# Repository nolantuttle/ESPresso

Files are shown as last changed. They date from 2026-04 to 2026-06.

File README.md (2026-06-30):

# ESPresso

Custom ESP32-C3 Supermini controller for the Gaggia Classic Pro. Handles boiler PID via SSR, shot timing, brew switch sense, and future pump PWM pressure profiling via MOC3021 + BTA41-600B TRIAC. Built with the Arduino framework.

## Hardware

| Component | Detail |
|---|---|
| MCU | ESP32-C3 Supermini (22×18mm, GPIOs 0–10, 20, 21) |
| Boiler control | Fotek 25DA SSR on GPIO10 via 330Ω |
| Thermocouple | MAX31855 on GPIOs 4 (SCK), 5 (MISO), 7 (CS) |
| Display | SSD1306 128×64 OLED on I2C, GPIOs 8 (SDA), 9 (SCL) |
| Pump control | MOC3021 + BTA41-600B TRIAC, GPIO2 PWM (pending MOC3041 + snubber) |
| Brew sense | Dry contact on second side of brew switch, GPIO1, 10kΩ pullup, active low |
| Pressure | XDB401 0–1.2MPa via 10kΩ/20kΩ divider → GPIO6 (not yet wired) |
| Mode toggle | Momentary to GND on GPIO20, firmware latched |
| Temp buttons | Resistor ladder on GPIO21 — up 10kΩ, down 47kΩ, 10kΩ pullup |
| Pot wiper | GPIO3, replacement pot coming (100nF cap to GND) |

# Electrical Schematic


## Firmware Features

- **Boiler PID** — Kp=38, Ki=4, Kd=250, 2s cycle time, SSR on GPIO10
- **Brew/steam modes** — toggle GPIO20; brew 185–220°F (default 205°F), steam 250–300°F (default 280°F)
- **Shot timer** — starts on brew switch close, stops on open, displayed live on OLED
- **Temp adjustment** — resistor ladder buttons ±1°F per press, long-press temp-up for settings stub
- **OLED** — mode, boiler state, current temp (large), setpoint, PID on-time, shot timer / error

## Pin Map

| GPIO | Function | Status |
|---|---|---|
| 0 | free | — |
| 1 | Brew switch sense | wired |
| 2 | MOC3041 PWM out | wired |
| 3 | free | — |
| 4 | MAX31855 SCK | wired |
| 5 | MAX31855 MISO | wired |
| 6 | Pressure transducer ADC | wired |
| 7 | MAX31855 CS | wired |
| 8 | OLED SDA | wired |
| 9 | OLED SCL | wired |
| 10 | SSR boiler out | wired |
| 20 | Mode toggle button | wired |
| 21 | Resistor ladder buttons | wired |

## Repository Contents
    /ESPresso    — Arduino sketch (ESP32-C3)
    /docs        — wiring notes and schematic

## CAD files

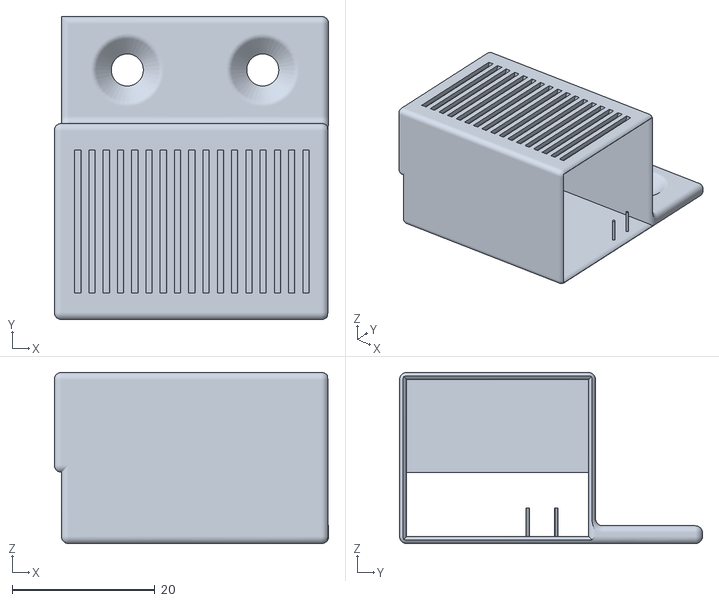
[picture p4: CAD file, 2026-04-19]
buck_module_case.STL
38.5 x 42.5 x 24.0

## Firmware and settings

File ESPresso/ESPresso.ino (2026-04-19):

#include <Wire.h>
#include <Adafruit_GFX.h>
#include <Adafruit_SSD1306.h>
#include <Adafruit_MAX31855.h>
#include <PID_v1.h>

// ─── Display ───────────────────────────────────────────────
#define SCREEN_WIDTH  128
#define SCREEN_HEIGHT 64
#define SCREEN_ADDRESS 0x3C
Adafruit_SSD1306 display(SCREEN_WIDTH, SCREEN_HEIGHT, &Wire, -1);

// ─── Pin definitions ───────────────────────────────────────
const int SPI_CLK_PIN  = 4;   // MAX31855 SCK
const int SPI_MISO_PIN = 5;   // MAX31855 DO
const int CS_PIN       = 7;   // MAX31855 CS
const int SDA_PIN      = 8;   // OLED SDA
const int SCL_PIN      = 9;   // OLED SCL
const int BOILER_PIN   = 10;  // SSR control
const int TOGGLE_PIN   = 20;  // Mode toggle button, pullup, closes to GND
const int ADC_BUTTONS  = 21;  // Resistor ladder: temp up (10kΩ) + temp down (47kΩ)
const int PUMP_PIN     = 2;   // MOC3021 PWM out
// const int ADC_POT      = 6;  // Pot wiper — not yet wired (pot snapped)
const int BREW_SENSE      = 1;   // Dry contact closure, 10kΩ pullup to 3.3V, active low
// const int ADC_PRESSURE = 2;  // Pressure transducer — not yet wired

// ─── Thermocouple ──────────────────────────────────────────
Adafruit_MAX31855 thermocouple(SPI_CLK_PIN, CS_PIN, SPI_MISO_PIN);

// ─── PID ───────────────────────────────────────────────────
// Kd bumped 180→280 to dampen 5-10F warmup overshoot
// If still overshooting: increase Kd toward 350-400
// If response near setpoint feels sluggish: back Kd toward 220
double BOILER_SETPOINT = 205.0;
double CURRENT_TEMP    = 0.0;
double PID_OUTPUT      = 0.0;
double Kp = 38, Ki = 4, Kd = 250;

unsigned long previousTime = 0;
unsigned long cycleTime    = 2000;
unsigned long offTime      = 0;
bool BOILER_ON             = false;

PID mainPID(&CURRENT_TEMP, &PID_OUTPUT, &BOILER_SETPOINT, Kp, Ki, Kd, DIRECT);

// ─── Mode ──────────────────────────────────────────────────
bool STEAM_ON = false;

const double BREW_SETPOINT_DEFAULT  = 205.0;
const double STEAM_SETPOINT_DEFAULT = 280.0;
const double BREW_SETPOINT_MIN      = 185.0;
const double BREW_SETPOINT_MAX      = 220.0;
const double STEAM_SETPOINT_MIN     = 250.0;
const double STEAM_SETPOINT_MAX     = 300.0;

// ─── Shot timer ────────────────────────────────────────────
bool brewActive                = false;
bool lastBrewRaw               = HIGH;
unsigned long brewStartTime    = 0;
unsigned long shotElapsed      = 0;   // ms, frozen at shot end
bool shotDone                  = false;

// ─── Display timing ────────────────────────────────────────
unsigned long lastDisplayUpdate      = 0;
const unsigned long DISPLAY_INTERVAL = 2000;

// ─── Button ladder ADC thresholds ──────────────────────────
// Temp up (left):     10kΩ to GND → ~1.65V → ADC ~2048
// Temp down (center): 47kΩ to GND → ~2.77V → ADC ~3440
// Nothing pressed:    floating high          → ADC ~4095
const int THRESH_TEMPUP_LO   = 1500;
const int THRESH_TEMPUP_HI   = 2600;
const int THRESH_TEMPDOWN_LO = 2700;
const int THRESH_TEMPDOWN_HI = 3800;

// ─── Button state ──────────────────────────────────────────
bool lastToggleRaw                 = HIGH;
unsigned long toggleDebounce       = 0;
const unsigned long TOGGLE_DEBOUNCE_MS = 50;

bool tempUpPressed                 = false;
bool tempDownPressed               = false;
unsigned long leftButtonHoldStart  = 0;
bool settingsStubFired             = false;
unsigned long lastTempUpDebounce   = 0;
unsigned long lastTempDownDebounce = 0;
const unsigned long DEBOUNCE_MS    = 50;
const unsigned long LONG_PRESS_MS  = 2000;

// ─── Setup ─────────────────────────────────────────────────
void setup() {

  Serial.begin(115200);

  Wire.begin(SDA_PIN, SCL_PIN);

  pinMode(CS_PIN, OUTPUT);
  digitalWrite(CS_PIN, HIGH);

  pinMode(BOILER_PIN, OUTPUT);
  digitalWrite(BOILER_PIN, LOW);

  pinMode(TOGGLE_PIN, INPUT_PULLUP);
  pinMode(BREW_SENSE, INPUT_PULLUP);

  ledcAttach(PUMP_PIN, 60, 8);

  mainPID.SetMode(AUTOMATIC);
  mainPID.SetOutputLimits(0, cycleTime);
  mainPID.SetSampleTime(1000);

  delay(500);

  if (!display.begin(SSD1306_SWITCHCAPVCC, SCREEN_ADDRESS)) {
    Serial.println(F("SSD1306 allocation failed"));
    for (;;);
  }

  startupScreen();
  delay(1500);
  display.clearDisplay();
}

void pumpOn(int duty){
  ledcWrite(PUMP_PIN, duty);
}

void pumpOff(){
  ledcWrite(PUMP_PIN, 0);
}

// ─── Loop ──────────────────────────────────────────────────
void loop() {
  readToggle();
  readButtons();
  readBrewSense();

  CURRENT_TEMP = thermocouple.readFahrenheit() - 10;

  mainPID.Compute();

  unsigned long now = millis();

  if (!BOILER_ON && now - previousTime >= cycleTime) {
    previousTime = now;
    offTime = now + (unsigned long)PID_OUTPUT;
    BOILER_ON = true;
    digitalWrite(BOILER_PIN, HIGH);
  }

  if (BOILER_ON && now >= offTime) {
    digitalWrite(BOILER_PIN, LOW);
    BOILER_ON = false;
  }

  unsigned long displayInterval = brewActive ? 500UL : DISPLAY_INTERVAL;
  if (now - lastDisplayUpdate >= displayInterval) {
    lastDisplayUpdate = now;
    mainDisplay();
  }
}

// ─── Toggle reading (GPIO20, firmware latched) ─────────────
void readToggle() {
  unsigned long now = millis();
  bool raw = digitalRead(TOGGLE_PIN);

  if (lastToggleRaw == HIGH && raw == LOW) {
    if (now - toggleDebounce > TOGGLE_DEBOUNCE_MS) {
      STEAM_ON = !STEAM_ON;
      BOILER_SETPOINT = STEAM_ON ? STEAM_SETPOINT_DEFAULT : BREW_SETPOINT_DEFAULT;
      resetPID();
      toggleDebounce = now;
    }
  }

  lastToggleRaw = raw;
}

// ─── Button ladder reading (GPIO21) ────────────────────────
void readButtons() {
  unsigned long now = millis();
  int raw = analogRead(ADC_BUTTONS);

  // Uncomment to debug ADC values:
  // Serial.println(raw);

  // ── Temp up (left button) ──
  bool tempUpNow = (raw >= THRESH_TEMPUP_LO && raw < THRESH_TEMPUP_HI);

  if (tempUpNow && !tempUpPressed) {
    leftButtonHoldStart = now;
    settingsStubFired = false;
    lastTempUpDebounce = now;
  }

  if (tempUpNow && !settingsStubFired) {
    if (now - leftButtonHoldStart >= LONG_PRESS_MS) {
      settingsStubFired = true;
      enterSettingsStub();
    }
  }

  if (!tempUpNow && tempUpPressed && !settingsStubFired) {
    if (now - lastTempUpDebounce > DEBOUNCE_MS) {
      adjustSetpoint(1.0);
    }
  }

  tempUpPressed = tempUpNow;

  // ── Temp down (center button) ──
  bool tempDownNow = (raw >= THRESH_TEMPDOWN_LO && raw < THRESH_TEMPDOWN_HI);

  if (tempDownNow && !tempDownPressed) {
    lastTempDownDebounce = now;
  }

  if (!tempDownNow && tempDownPressed) {
    if (now - lastTempDownDebounce > DEBOUNCE_MS) {
      adjustSetpoint(-1.0);
    }
  }

  tempDownPressed = tempDownNow;
}

// ─── Setpoint adjustment ───────────────────────────────────
void adjustSetpoint(double delta) {
  BOILER_SETPOINT += delta;
  if (STEAM_ON) {
    BOILER_SETPOINT = constrain(BOILER_SETPOINT, STEAM_SETPOINT_MIN, STEAM_SETPOINT_MAX);
  } else {
    BOILER_SETPOINT = constrain(BOILER_SETPOINT, BREW_SETPOINT_MIN, BREW_SETPOINT_MAX);
  }
}

// ─── PID reset ─────────────────────────────────────────────
void resetPID() {
  mainPID.SetMode(MANUAL);
  PID_OUTPUT = 0;
  mainPID.SetMode(AUTOMATIC);
}

// ─── Settings stub ─────────────────────────────────────────
void enterSettingsStub() {
  // TODO: implement settings menu
  // Suggested: Kp, Ki, Kd tuning, brew/steam setpoint defaults,
  // PID cycle time, temp offset calibration
  Serial.println(F("Settings mode triggered (not yet implemented)"));
}

// ─── Brew sense + shot timer (GPIO1, active low) ───────────
void readBrewSense() {
  bool raw = digitalRead(BREW_SENSE);

  if (lastBrewRaw == HIGH && raw == LOW) {
    brewActive = true;
    brewStartTime = millis();
    shotDone = false;
    pumpOn(180); // start pump immediately on switch close
} else if (lastBrewRaw == LOW && raw == HIGH) {
    brewActive = false;
    shotElapsed = millis() - brewStartTime;
    shotDone = true;
    pumpOff(); // stop pump immediately on switch open
}

  lastBrewRaw = raw;
}

// ─── Startup screen ────────────────────────────────────────
void startupScreen() {
  display.clearDisplay();
  display.setTextColor(SSD1306_WHITE);
  display.setTextSize(2);
  display.setCursor(10, 10);
  display.println(F("ESPresso"));
  display.setTextSize(1);
  display.setCursor(28, 38);
  display.println(F("warming up..."));
  display.display();
}

// ─── Main display ──────────────────────────────────────────
void mainDisplay() {
  display.clearDisplay();
  display.setTextColor(SSD1306_WHITE);

  // Mode header
  display.setTextSize(1);
  display.setCursor(0, 0);
  display.printf("Mode: %s", STEAM_ON ? "STEAM" : "BREW");

  // Boiler indicator
  display.setCursor(90, 0);
  display.print(BOILER_ON ? "[ON] " : "[OFF]");

  // Divider
  display.drawLine(0, 10, 127, 10, SSD1306_WHITE);

  // Current temp large
  display.setTextSize(2);
  display.setCursor(0, 16);
  display.printf("%.1fF", CURRENT_TEMP);

  // Setpoint
  display.setTextSize(1);
  display.setCursor(0, 38);
  display.printf("Set:  %.1fF", BOILER_SETPOINT);

  // PID on time
  display.setCursor(0, 48);
  display.printf("OnT:  %lums", (unsigned long)PID_OUTPUT);


  // Shot timer / delta
  display.setCursor(0, 56);
  if (brewActive) {
    unsigned long s = (millis() - brewStartTime) / 1000;
    display.printf("Shot: %lus [>>>]", s);
  } else if (shotDone) {
    display.printf("Shot: %.1fs", shotElapsed / 1000.0);
  } else {
    double delta = BOILER_SETPOINT - CURRENT_TEMP;
    display.printf("Err:  %+.1fF", delta);
  }

  display.display();
}

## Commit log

2026-04-19 ESP32C3 Supermini overhaul
    [Gagietto.kicad_sch, buck_module_case.STL]
2026-04-20 Update electrical schematic in README
    Updated the electrical schematic section in README.md.
